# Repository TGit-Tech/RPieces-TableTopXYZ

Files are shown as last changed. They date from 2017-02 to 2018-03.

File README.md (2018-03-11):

-----------------------------------------------------------------------------------
# RPieces-TableTopXYZ
-----------------------------------------------------------------------------------
A Simple and Printable TableTop XYZ Motion Frame using 28BYJ-48 Unipolar Stepper
Motors.

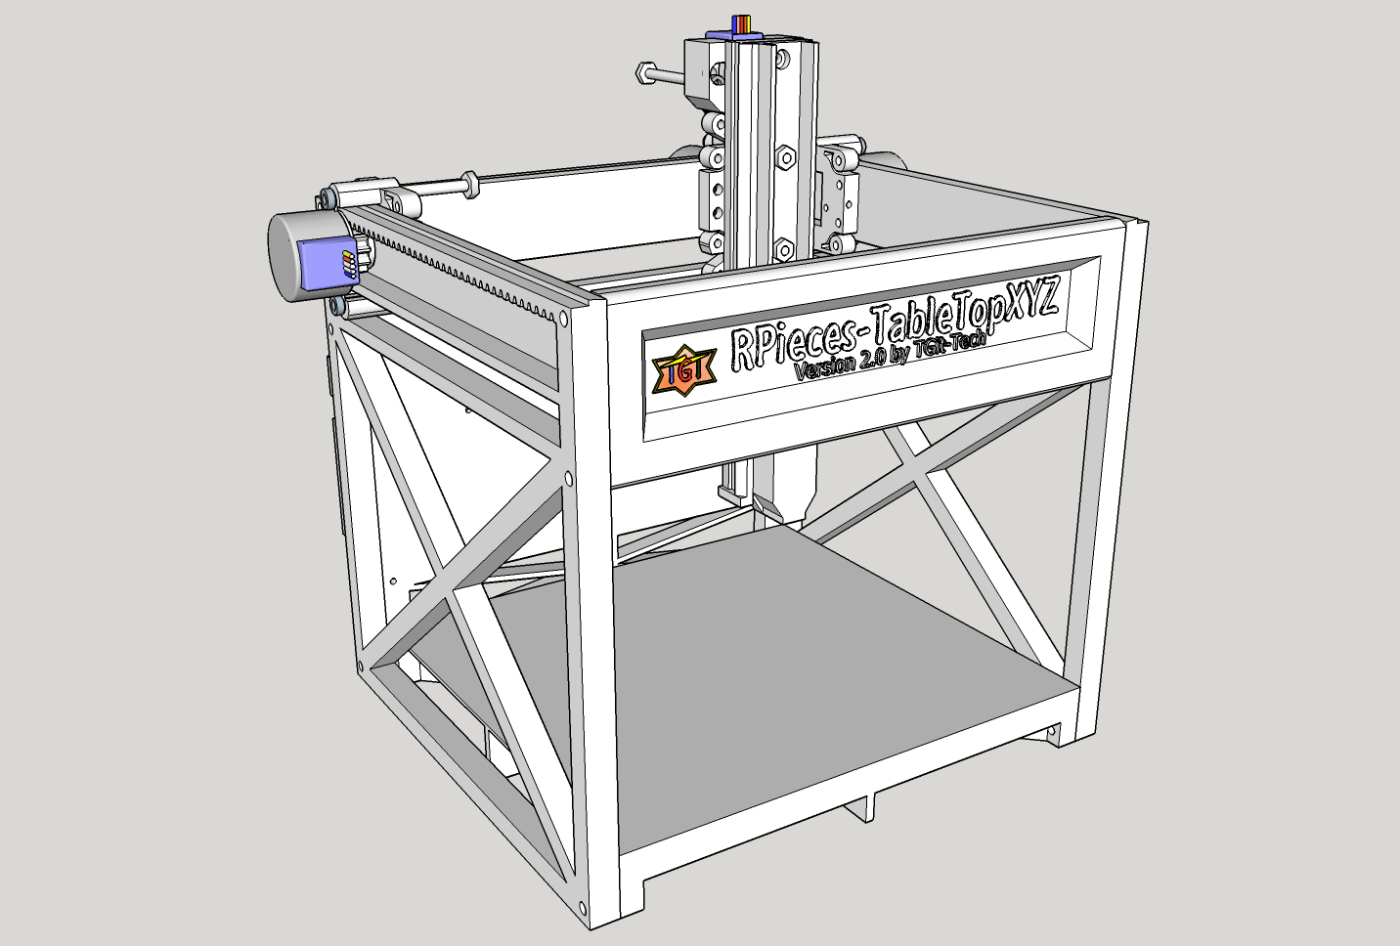
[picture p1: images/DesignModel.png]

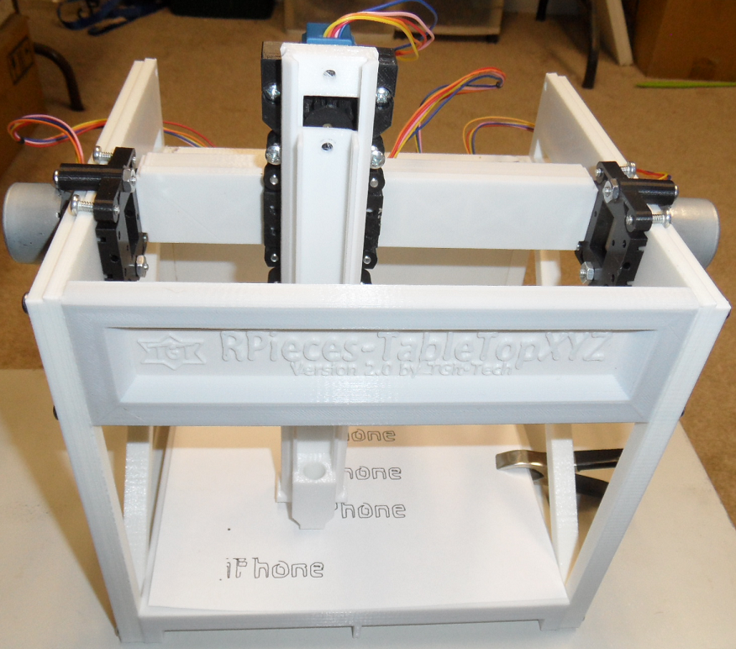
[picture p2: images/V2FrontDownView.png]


The RPieces TableTopXYZ Frame is a project that will attempt to create a simple one
day build of an all in one 3D Printer, Mill, and Plotter.  The project will minimize
the use of linear bearings in place of 3D Printed Rails and minimize the use of 
timing belts in place of 3D-Printed Pinions ( Thus the R.=Rack & P.=Pinion 
abbreviation in RPieces naming convention )

Example Video @ https://www.youtube.com/watch?v=2BT0keDggYo

-----------------------------------------------------------------------------------
#Project Status
-----------------------------------------------------------------------------------
This is RPieces-TableTopXYZ Version 2.0 Beta;  Version 1.0 was released previously.
Unless issues occur this will be the final Version 2.0

Version 2.0 enhancements include a much more stable frame & carriages.  As can be
seen by the video; the prints are still quite sloppy but the test model was printed
using extremely soft plastic on the carriages.  I'd suggest a little harder plastic
on the carriages than originally suggested in the User Manual.

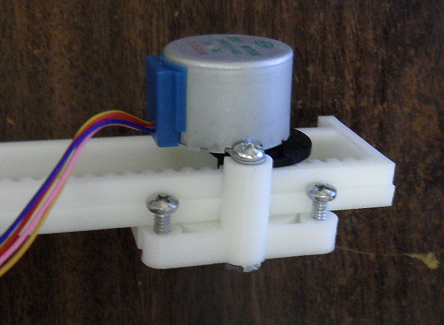
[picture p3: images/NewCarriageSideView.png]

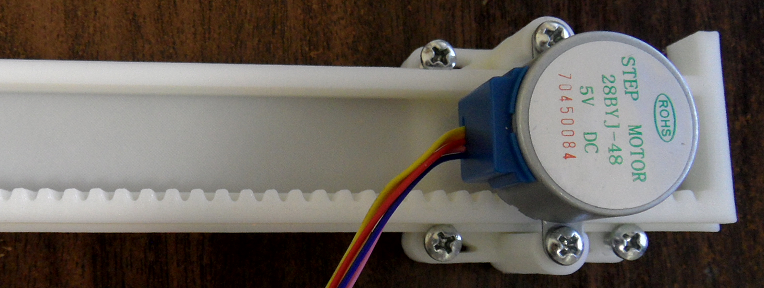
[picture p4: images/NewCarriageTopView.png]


-----------------------------------------------------------------------------------
#Cost and Materials
-----------------------------------------------------------------------------------
Building this project requires

    - (1) 3D Printer with a build surface of at least 190mm x 190mm   ... $N/A
    - (1) Arduino UNO or NANO / half breadboard / jumper kit          ... $ 6.95
    - (4) 28BYJ-48 Stepper Motors with ULN2003 Drivers                ... $ 9.90
    - (~20) Male to Female Dupont jumpers                             ... $ 1.60
    - (1) 5Vdc Wall-module Power Supply adapter at ~2A                ... $ 2.15
    - (12) #6-32 x 1/2" Long Machine Screws                           ... $ 0.24
    - (10) #6-32 x 3/4" Long Machine Screws                           ... $ 0.20
    - (8) #6-32 x 1-1/2" Long Machine Screws                          ... $ 0.16
    - (7) #6-32 x 3/4" Long Machine Screws                            ... $ 0.14
    - (2) #6-32 x 1-1/2" Long Machine Screws                          ... $ 0.06
    - (24) #6 x 3/4" Sheet Metal Screws                               ... $ 0.48
    - (20) #4 x 3/8" Sheet Metal Screws                               ... $ 0.40
    - (10) Corresponding hex nuts (#6) for machine screws             ... $ 0.20
    - Modified GRBL Firmware @ https://github.com/tgit23/GRBL-28byj-48
    - Grbl Controller Software @ http://zapmaker.org/projects/grbl-controller-3-0/

TOTAL ESTIMATED COST (including filament): $33.93
Detailed items/cost inside the Assembly document linked below.

-----------------------------------------------------------------------------------
#Getting Started
-----------------------------------------------------------------------------------
Assembly document can be found @ https://github.com/tgit23/RPieces-TableTopXYZ/blob/master/docs/RPieces-TableTopXYZ-Version2-User-Assembly.pdf

I.e. /docs/RPieces-TableTopXYZ-Version2-User-Assembly.pdf

Before trying to control the model;  Setup the parameters of 'grbl' firmware through
the 'grbl controller' command interface by entering the following commands.

    - $0=30
    - $100=100
    - $101=100
    - $102=100
    - $110=550
    - $111=550
    - $112=550
    - $120=100
    - $121=100
    - $122=100
    
You can now load a file from the \nc-examples folder into grbl controller for unit
testing.

-----------------------------------------------------------------------------------
CONTRIBUTING
-----------------------------------------------------------------------------------
Anyone interested in joining this project can email
tgit28@gmail.com with a return email address.  Details of what can
be done and what needs done can be negotiated from there.

We'd really appreciate any extra man-power we can gather..

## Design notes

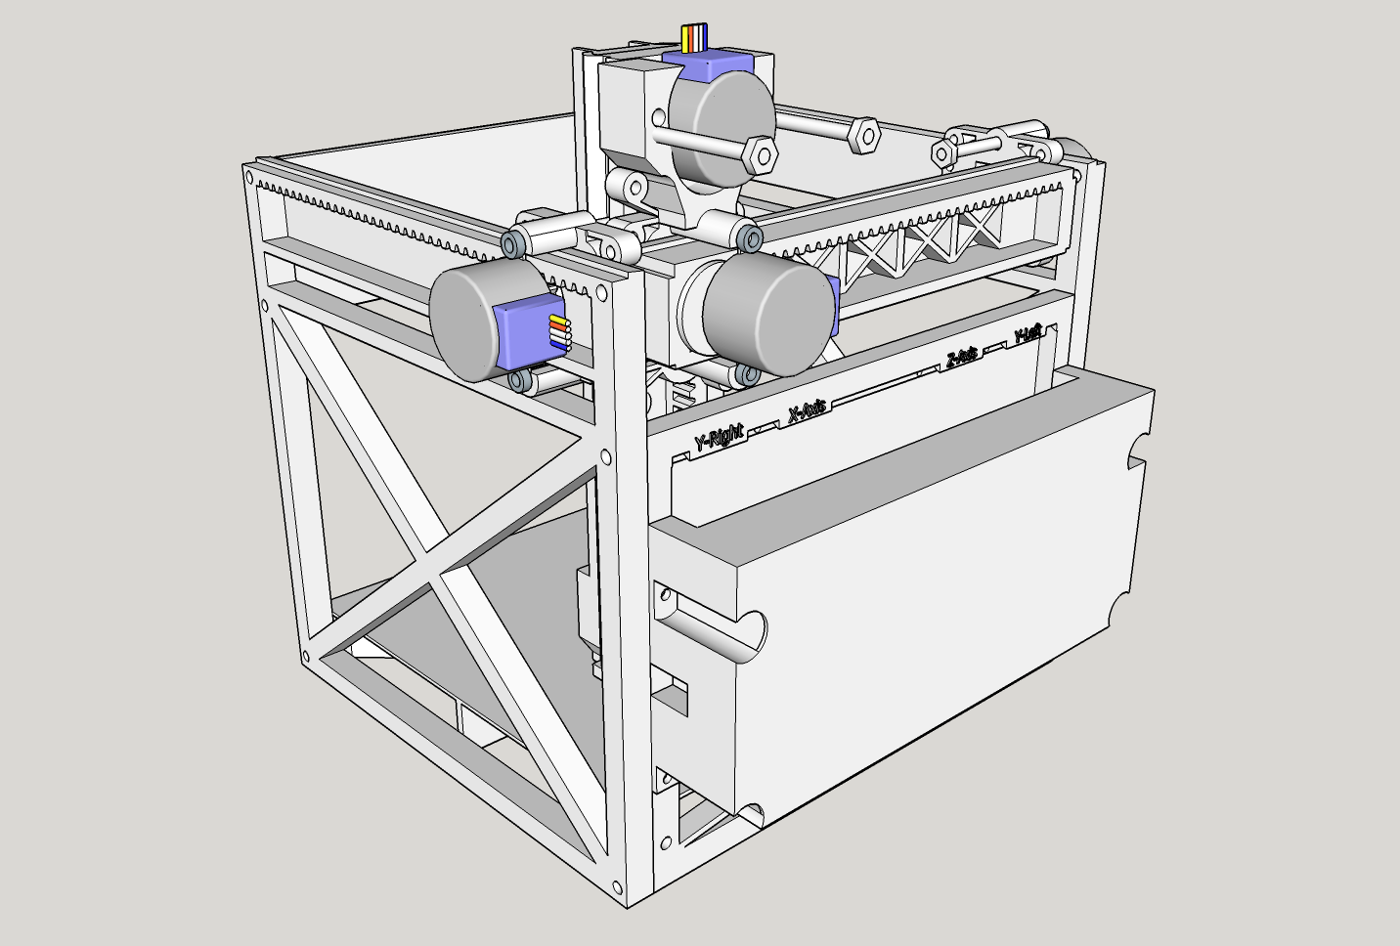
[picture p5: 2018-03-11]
images/DesignModel-Back.png

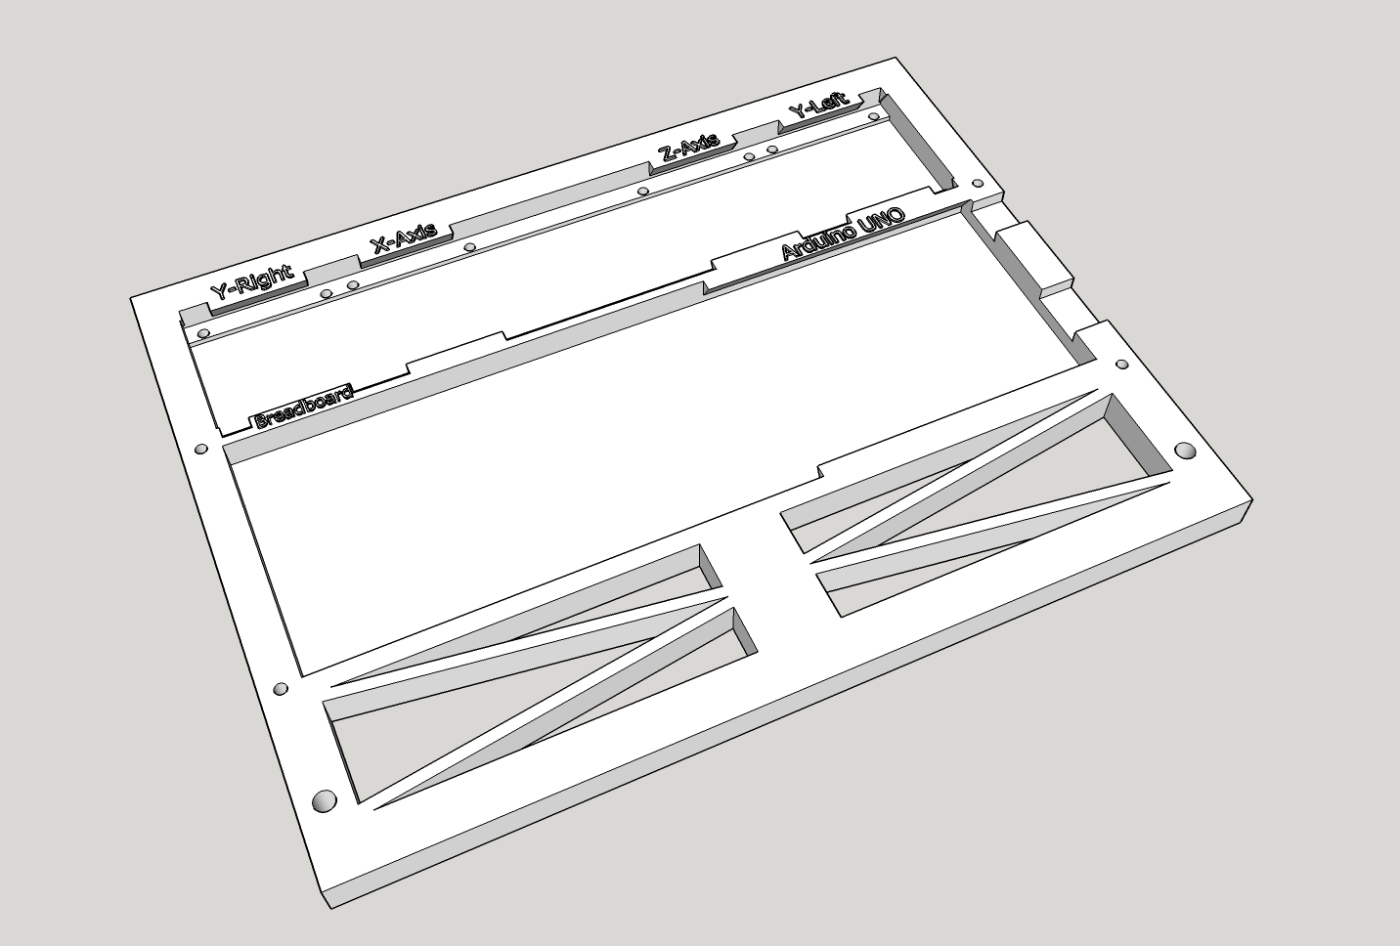
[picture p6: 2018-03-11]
images/Back.png

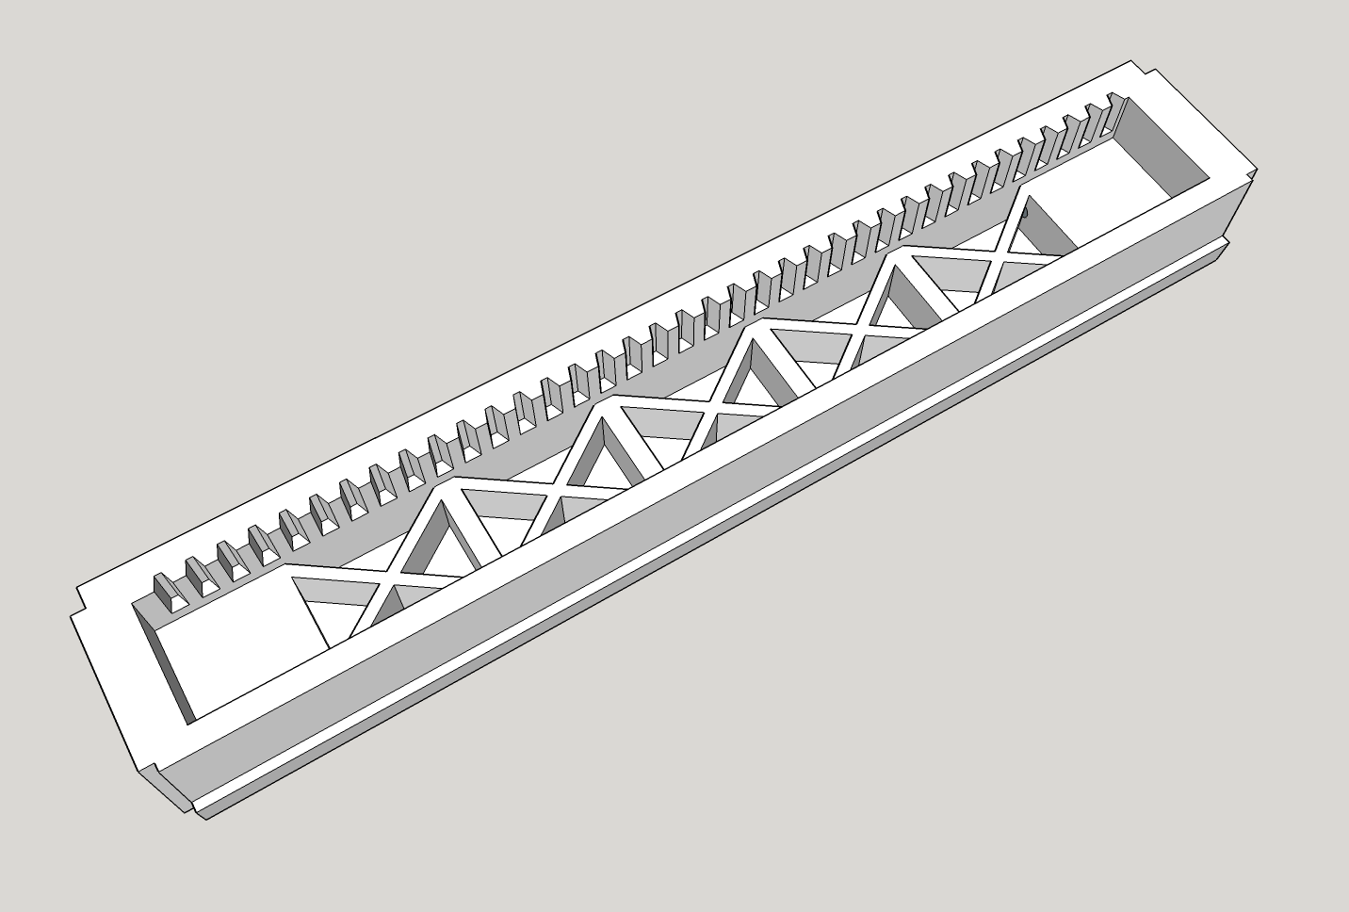
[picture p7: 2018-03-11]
images/X-Rack.png

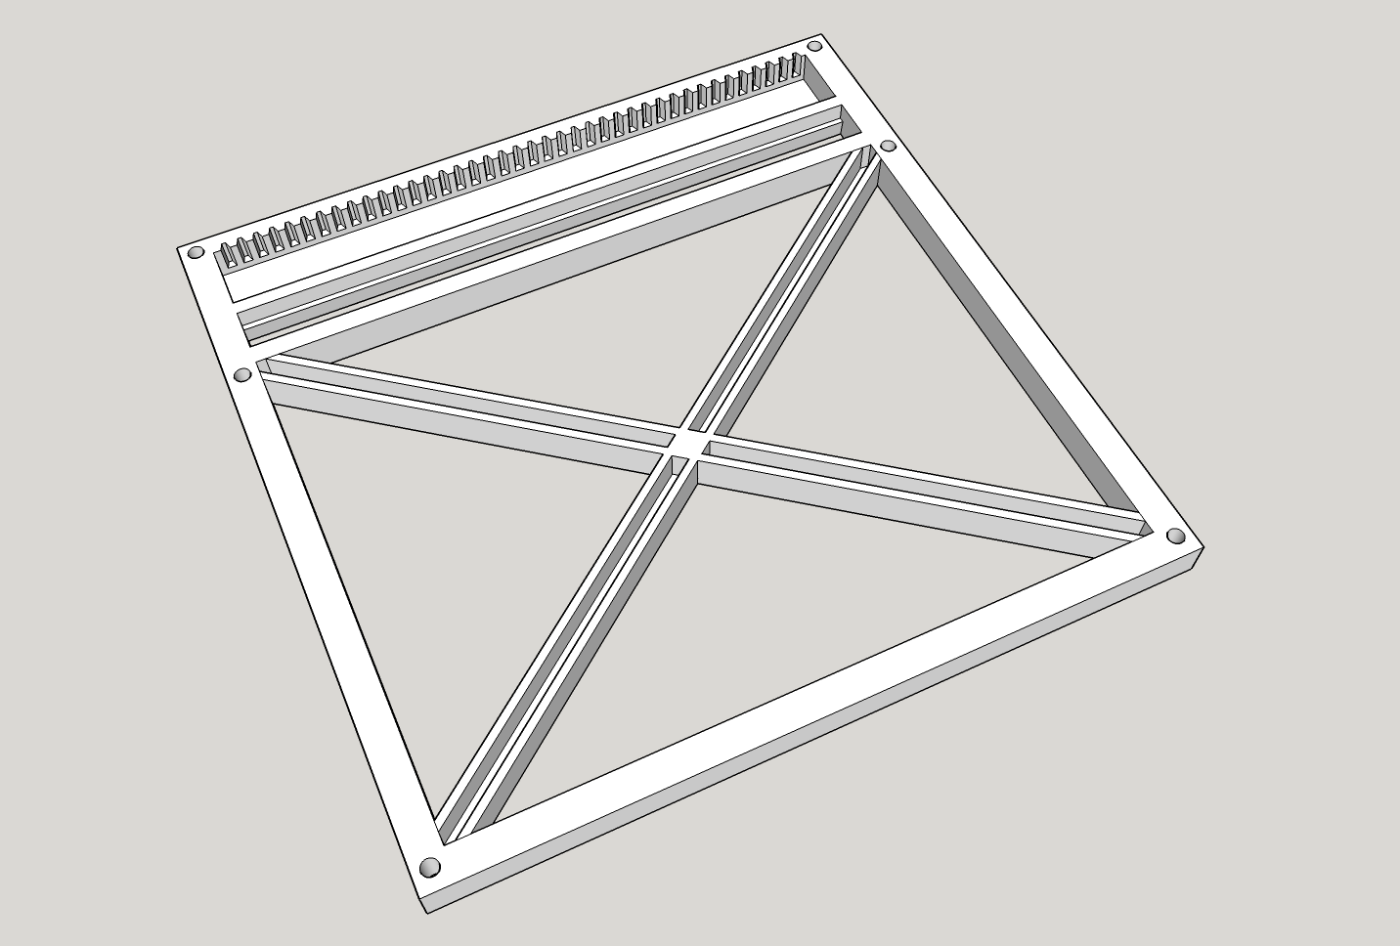
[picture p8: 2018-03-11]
images/Side.png

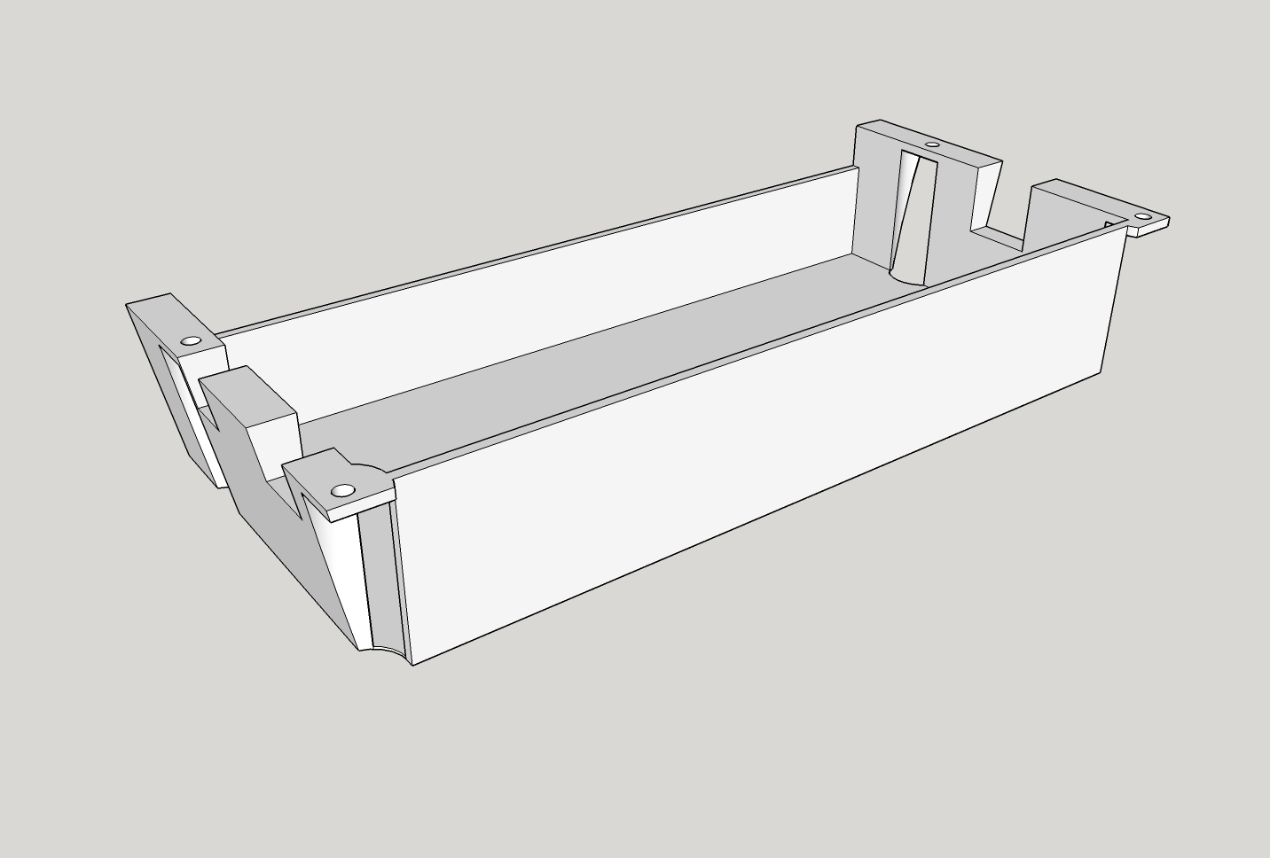
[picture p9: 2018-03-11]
images/BackCover.png

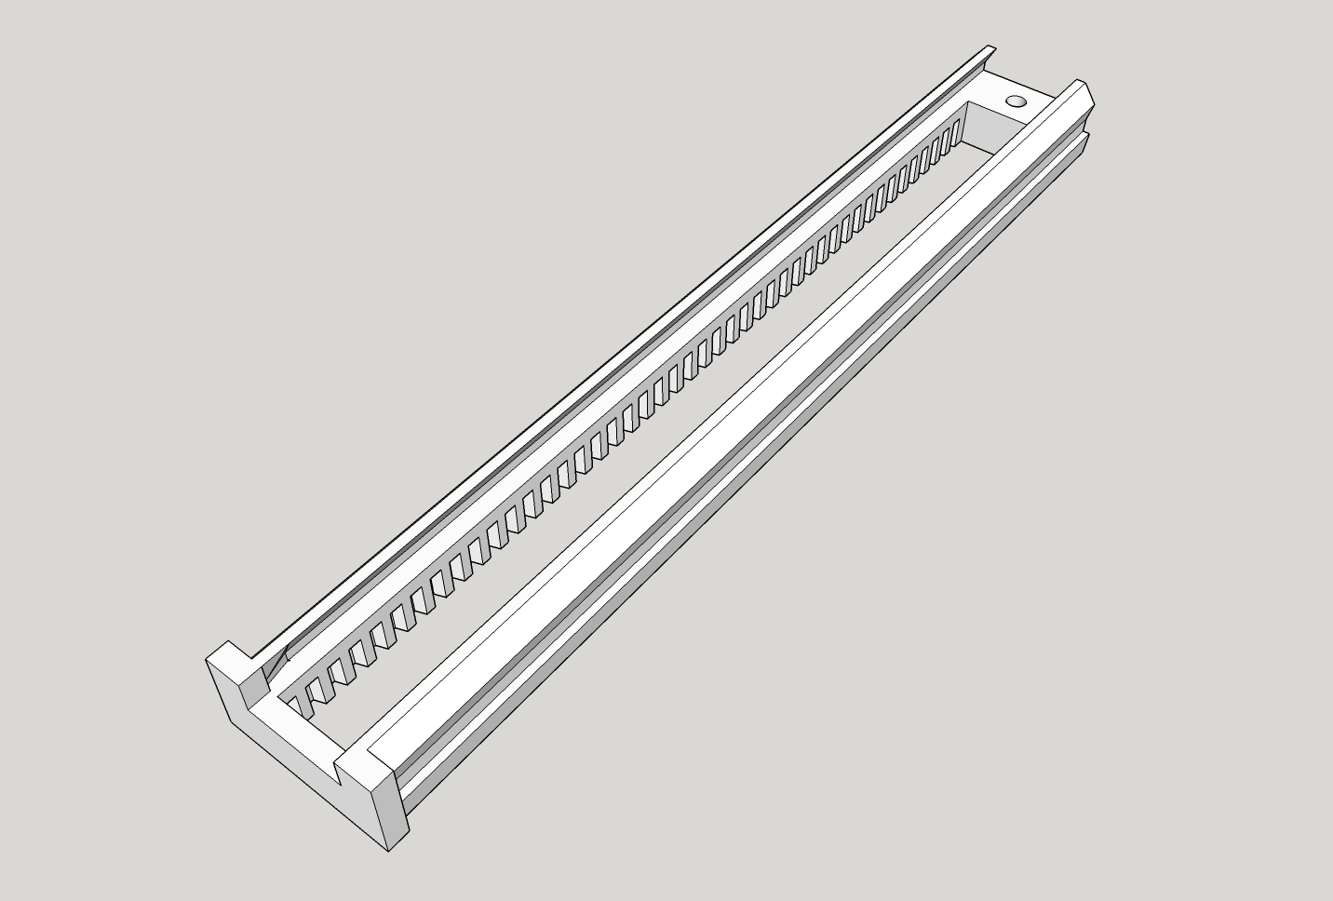
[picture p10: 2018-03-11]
images/Z-Rack.png

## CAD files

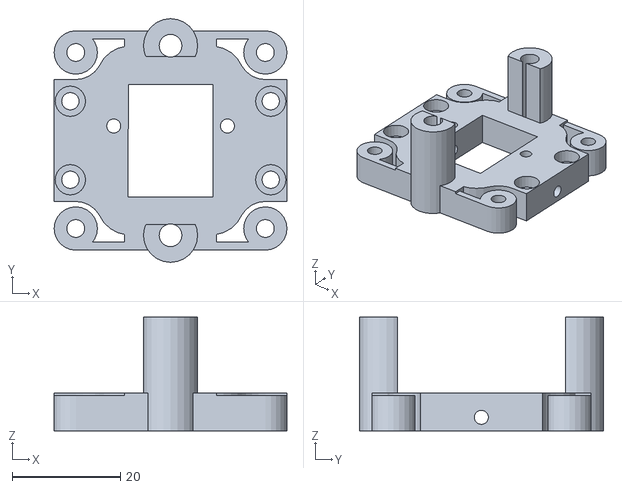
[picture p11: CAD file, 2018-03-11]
Pieces-STL/Y-Carriage.stl
43.0 x 45.0 x 21.0

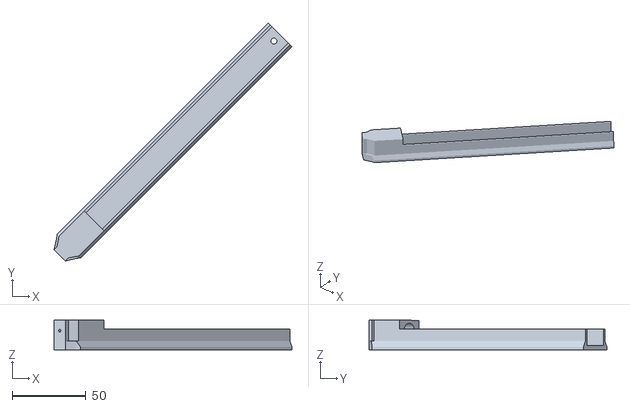
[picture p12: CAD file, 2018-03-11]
ToolHeads-STL/ToolHead-PilotRazorPointPen.stl
161.1 x 161.1 x 20.0

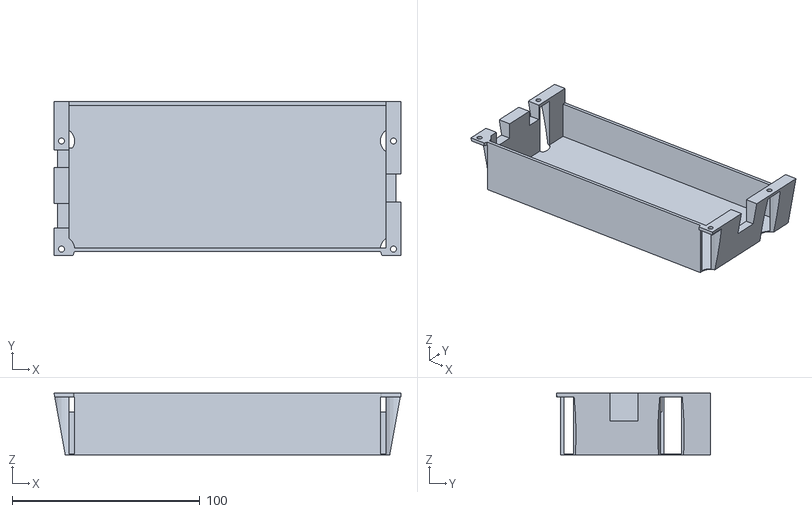
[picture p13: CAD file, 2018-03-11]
Pieces-STL/BackCover.stl
185.0 x 82.0 x 33.0

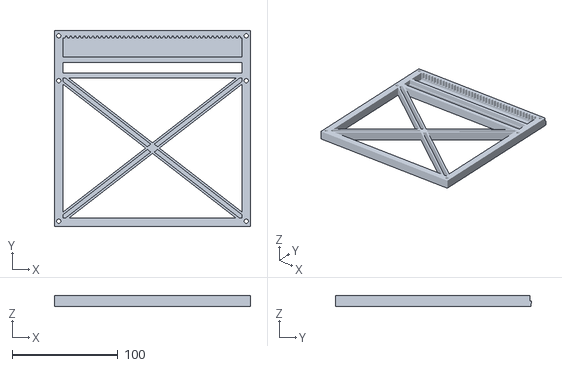
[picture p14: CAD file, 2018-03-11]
Pieces-STL/Side.stl
185.0 x 185.0 x 10.0

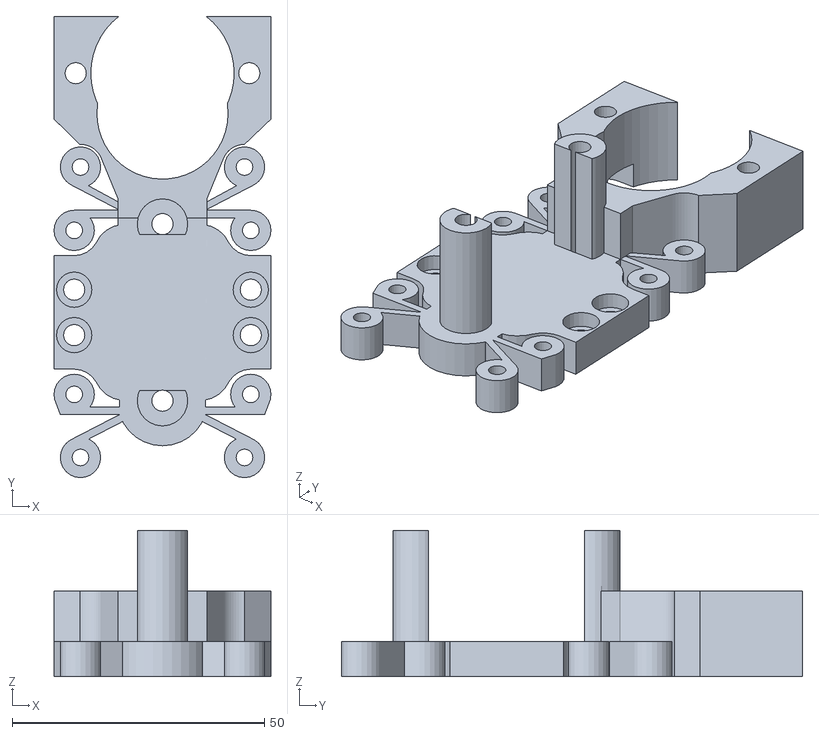
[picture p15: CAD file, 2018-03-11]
Pieces-STL/XZ-Carriage.stl
43.0 x 91.4 x 29.0

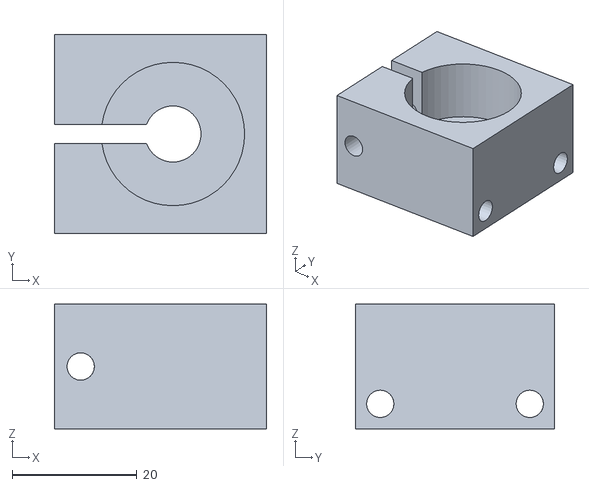
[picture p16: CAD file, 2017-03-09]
ToolHeads-STL/ToolHead-MiniDrill.stl
34.0 x 32.0 x 20.0

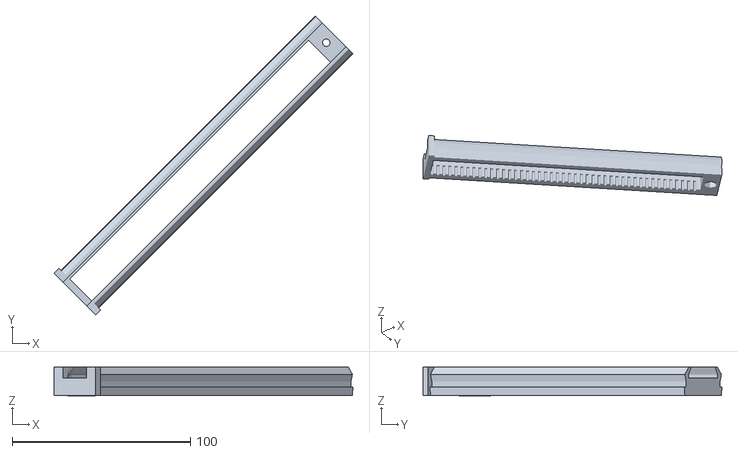
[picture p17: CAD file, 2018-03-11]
Pieces-STL/Z-Rack.stl
167.9 x 167.9 x 16.0

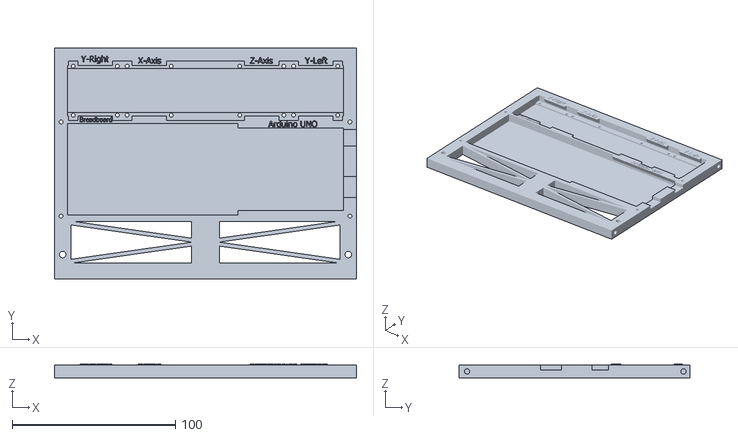
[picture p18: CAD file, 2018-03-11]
Pieces-STL/Back.stl
185.0 x 141.6 x 8.50

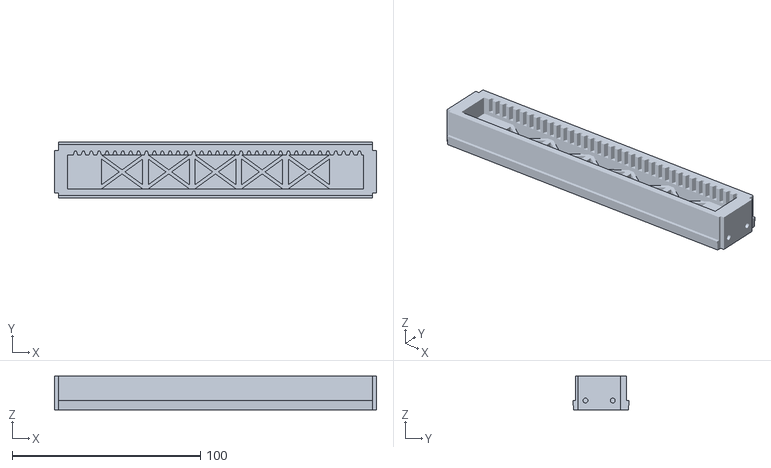
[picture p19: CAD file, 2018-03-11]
Pieces-STL/X-Rack.stl
171.0 x 30.0 x 18.0

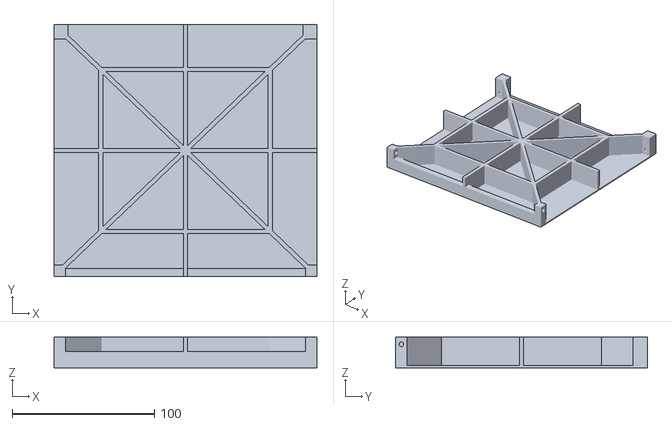
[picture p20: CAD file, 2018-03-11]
Pieces-STL/Bottom.stl
185.0 x 177.0 x 21.5

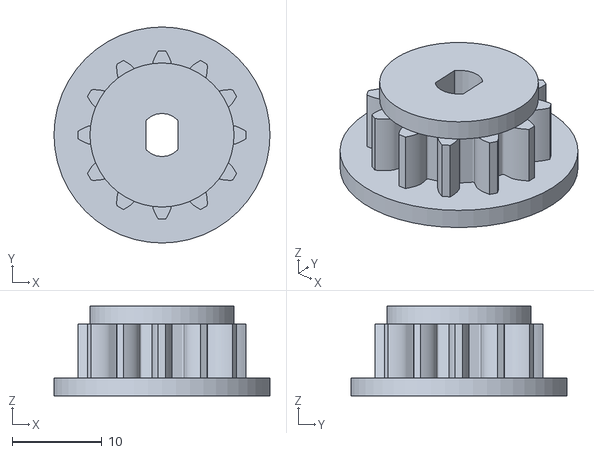
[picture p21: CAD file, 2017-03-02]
Pieces-STL/MotorGear.stl
24.0 x 24.0 x 10.0

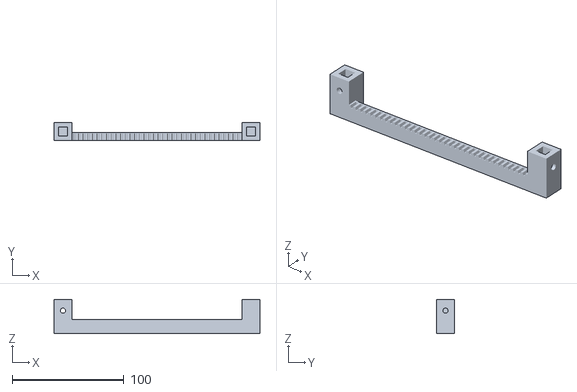
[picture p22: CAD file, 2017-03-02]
Pieces-STL/Y-Rack-Left.stl
184.0 x 16.0 x 30.5

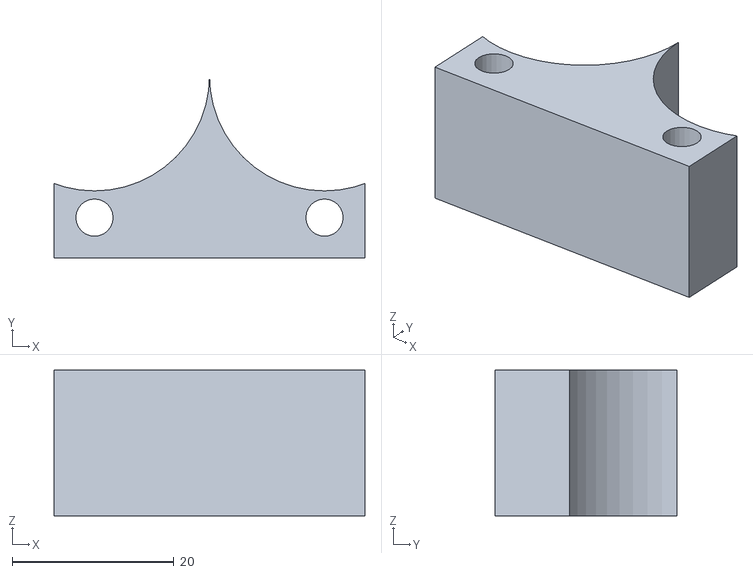
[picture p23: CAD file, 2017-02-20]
Pieces-STL/XYMotorTie.stl
38.4 x 22.5 x 18.0

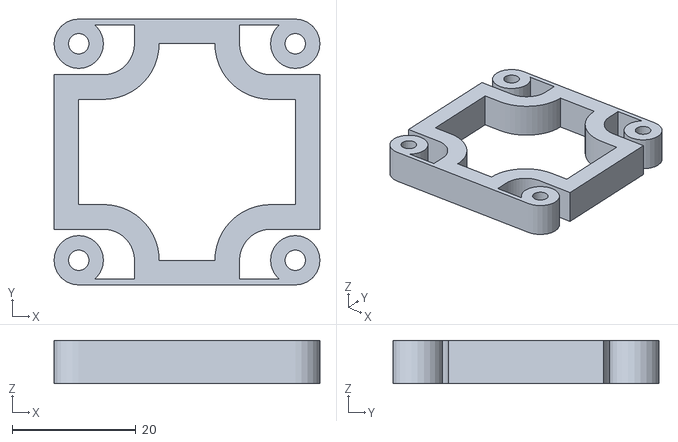
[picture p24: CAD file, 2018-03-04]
ToolHeads-STL/ScrewHead-Slider.stl
43.0 x 43.0 x 7.00

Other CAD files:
ToolHeads-STL/ScrewHead-Rail.stl
Pieces-SketchUp/Back.skp
Pieces-SketchUp/BackCover.skp
Pieces-SketchUp/Bottom.skp
Pieces-SketchUp/Front.skp
Pieces-SketchUp/MotorGear.skp
Pieces-SketchUp/Side.skp
Pieces-SketchUp/X-Rack.skp
Pieces-SketchUp/XZ-Carriage.skp
Pieces-SketchUp/Y-Carriage.skp
Pieces-SketchUp/Z-Rack.skp
ToolHeads-SketchUp/ScrewHead-Rail.skp
ToolHeads-SketchUp/ScrewHead-Slider.skp
ToolHeads-SketchUp/ToolHead-MiniDrill.skp
ToolHeads-SketchUp/ToolHead-PilotRazorPointPen.skp
ToolHeads-SketchUp/ToolHead-Template.skp
docs/DesignModel.skp

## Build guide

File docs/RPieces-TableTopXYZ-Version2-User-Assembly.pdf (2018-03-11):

# RPieces - TableTopXYZ

## User and Assembly Manual

For Version 2.0

Written By: TGit-Tech (03/2018) Feel free to use: no strings attached (text content only / images respectfully referenced)

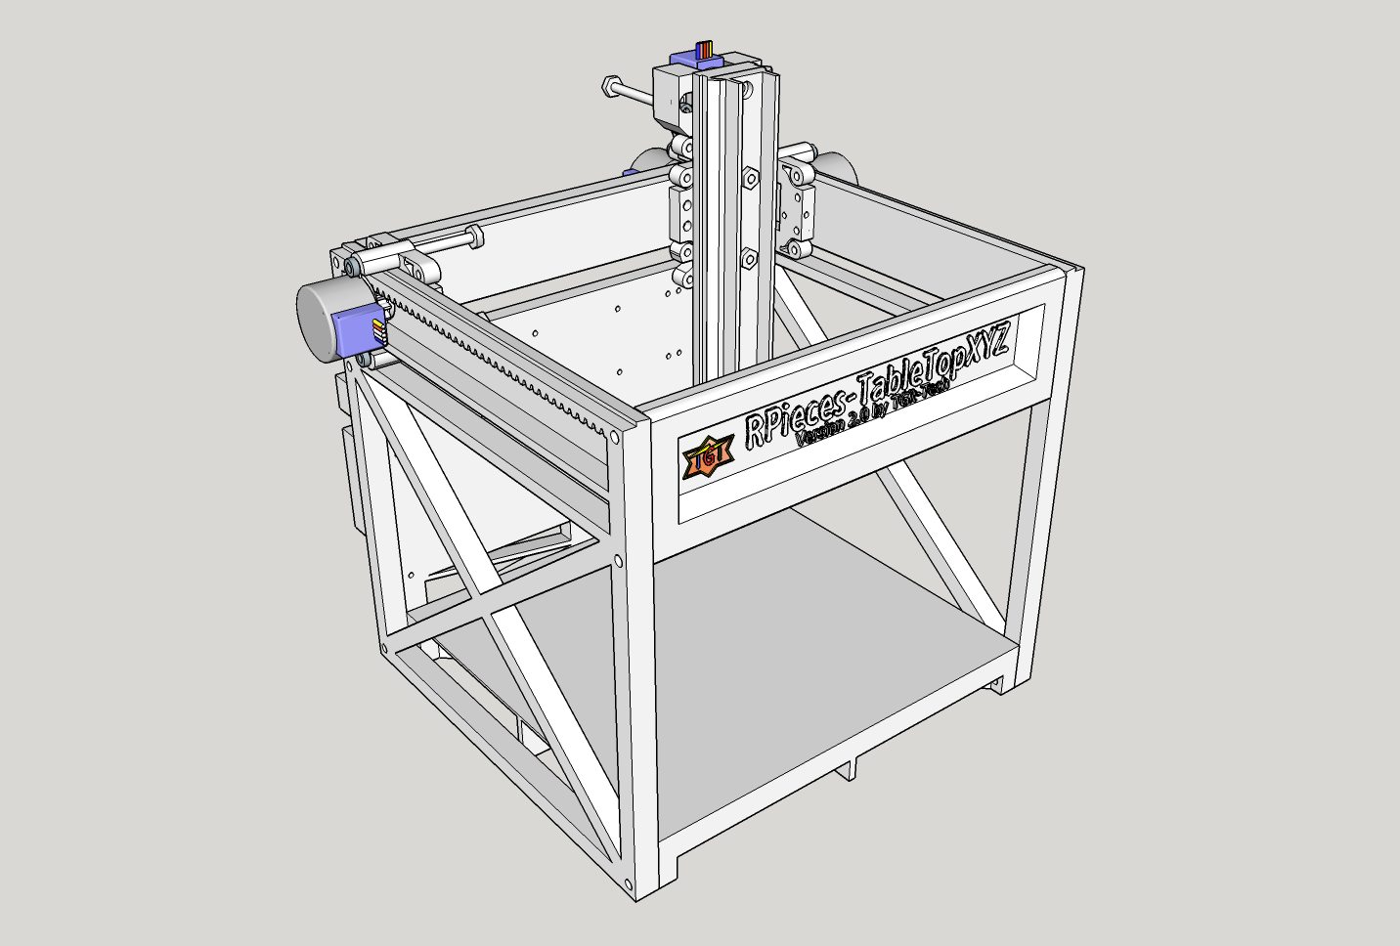
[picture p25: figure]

# Table of Contents

( 1. INTRODUCTION :: INTRODUCTION :: INTRODUCTION ) Page -2-

### 1. INTRODUCTION

The “RPieces – TableTopXYZ ” project's goal is to provide a simple and almost entirely printable motion frame for various usages. Possibly including 3d printing, plotting and minor milling. The platform can also be used in testing software, firmware or just testing model-creation on a physical unit before sending it to a much larger commercial unit.

The project is Open Source and Resides at: https://github.com/TGit-Tech/RPieces-TableTopXYZ
This documentation resides at: https://github.com/TGit-Tech/RPieces-TableTopXYZ/tree/master/docs

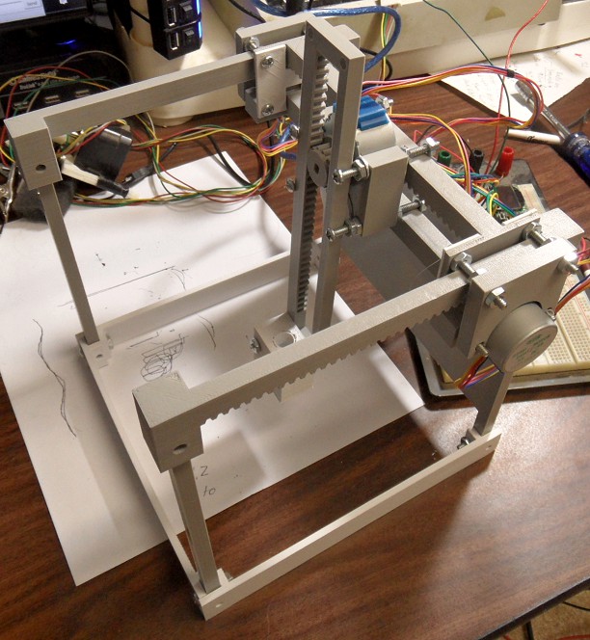
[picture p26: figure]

( 2. BILL OF MATERIALS - $33.93 :: BILL OF MATERIALS - $33.93 :: BILL OF MATERIALS - $33.93 ) Page -3-

### 2. BILL OF MATERIALS - $33.93

### 2.1 Tools (N/A)

The following tools are required to build the project components
✔ 3D-Printer ( With a 185mm x 185mm or larger XY Build Envelope ) ✔ Phillips head screw driver and 5/16 nut driver or wrench

### 2.2 Power Supply ( $2.15 )

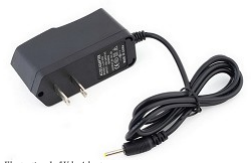
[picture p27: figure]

Illustration 1: 5Vdc Adapter

✔ ( 1 ) 5Vdc ( Possibly up to 7Vdc – I'm using a 6Vdc 700mA ) Power Adapter @ 400mA or greater ( $2.15 )
◌ https://www.aliexpress.com/item/1pcs-Universal-for-IC-Power-Adapter-AC-Charger-5V-2A-DC-2-5mm-US-for-Android/32581666097.html

### 2.3 Electronic Control ( $18.45 )

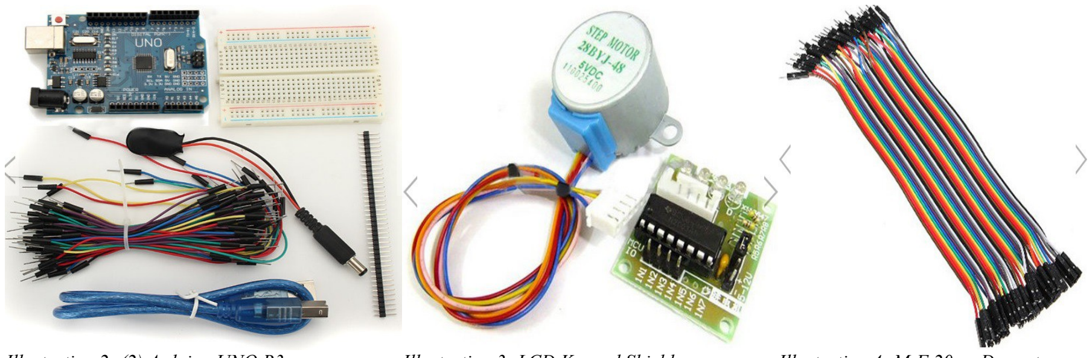
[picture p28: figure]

Illustration 2: (2) Arduino UNO R3 | Illustration 3: LCD Keypad Shield | Illustration 4: M-F 20cm Dupont

✔ ( 1 ) UNO R3 or NANO Atmega328P Module, Mini Breadboard & Jumpers ( $6.95/ea )
◌ https://www.aliexpress.com/item/Starter-Kit-for-Uno-R3-Bundle-of-5-Items-Uno-R3-Breadboard-Jumper-Wires-USB-Cable/32813470187.html

✔ ( 4 ) 28BYJ-48 5V DC Step Motor with ULN2003 Driver Board ( $9.90/per5 )
◌ https://www.aliexpress.com/item/NEW-5pcs-lot-Gear-Stepper-Motor-28BYJ-48-DC-5V-ULN2003-Driver-Test-Module-Board-For/32826285578.html ◌ Resources
- 28BYJ Data-sheet http://www.sensors.co.nz/datasheet/28BYJ-48%20Stepper%20Motor.pdf
- ULN2003 Data-sheet http://www.ti.com/lit/ds/symlink/uln2003a.pdf

✔ ( ~40 ) 20 cm Male to Female DuPont Jumpers ( $1.60 )
◌ https://www.aliexpress.com/item/Dupont-line-40pcs-20cm-male-to-female-jumper-wire-Banana-pro-Dupont-cable-support-Raspberry-pi/32393258299.html

2.4 3D Parts & Fasteners ($13.33)

Below is the list of the Parts that need to be printed with a 3D-Printer in the order of assembly; so you can print them in the order shown and assemble them as they finish. Default printer settings are below; but check the per-part details below for any part-specific setting if one may exist .

✔ Parts were printed on an Anet A8 3D-Printer using Cura with the following settings
◌ Layer Height = 0.2

( 2.4 BILL OF MATERIALS - $33.93 :: 3D Parts & Fasteners ($13.33) :: 3D Parts & Fasteners ($13.33) ) Page -4-

◌ Shell Thickness = 1.6
◌ Fill Density = 100%
◌ Print Speed = 60
◌ Support = None

✔ Suggestions
◌ Bed leveling is extra important with any Rack-Gear containing prints -- to ensure a fairly consistent width across the entire tab-out. ◌ Use hairspray, tape or any preferred method that keeps large prints on the build plate – uneven builds will cause massive faults.
◌ Parts that hold structure are PLA preferred due to its non-curling and non-flexible (brittle) attributes.
- I've especially been impressed with iFun and PxMallion for cheap structurally sound PLA filament brands
◌ Carriage parts are ABS preferred due to their flexible tension-ed slide screws but PLA should work fine.
- eSun PLA+ filament makes a nice balance between PLA and ABS for such parts.
◌ Push all stepper motors towards the drive rail before tightening -- to make a snug gear to rail connection ( reduces slop ).
QTY | Part Picture Part Filename Grams of Filament | Attaches To | Fasteners (!Per-Part!)*QTY | Est. Costs Per-Part PLA Cost @ $15/Kg roll www.boltdepot.com @100-lots | Total Cost
4 | MotorGear.stl 3-grams PLA preferred | 28BYJ-Motor | N/A – Pressed On | $0.04 Plastic | $0.18
1 | X-Rack.stl 58-grams PLA preferred | N/A | N/A See XZ & Y-Carriage | $0.87 Plastic | $0.87
1 | XZ-Carriage.stl 30-grams ABS preferred | X-Rack X-Motor Z-Rack Z-Motor | (4)#6 x 3/4” Sheet Metal Screws [$0.02/ea] (2)#6-32 x 1.5” [$0.03/ea] (4)#6-32 x 1/2” [$0.02/ea] (2)#6-32 x 3/4” [$0.02/ea] | $0.45 Plastic $0.26 Fasteners | $0.71
2 | Y-Carriage.stl 12-grams ABS preferred | X-Rack Full-Side Y-Motor | (2)#4 x 3/4” Sheet Metal Screws [$0.03/ea] (4)#6-32 x 1/2” Machine Screws [$0.02/ea] (2)#6-32 x 1” Machine Screws [$0.03/ea] | $0.18 Plastic $0.20 Fasteners | $0.76

Assembly Instructions for parts above @ #3.1.XZ-Carriage|outline
1 | Back.stl 109-grams PLA preferred | (4)ULN2003 Arduino (2)Side | (16) #4 x 3/8” Sheet Metal Screws [$0.02/ea] [Optional] – Attaching ULN2003 with screws makes them much more stable but not required. N/A See Side for fasteners | $1.63 Plastic $0.32 Fasteners | $1.95
1 | BackCover.stl [!Optional Part!] 54-grams W/Supports! | Back | (4)#4 x 3/8” Sheet Metal Screws [$0.02/ea] | $0.81 Plastic $0.08 Fasteners | $0.89

Assembly Instructions for parts above @ #4.ELECTRONICS|outline 1

Front.stl
60-grams

(2)Side N/A See Side for fasteners

$0.90 Plastic
$0.08 Fasteners

$0.98

( 2.4 BILL OF MATERIALS - $33.93 :: 3D Parts & Fasteners ($13.33) :: 3D Parts & Fasteners ($13.33) ) Page -5-

| PLA preferred
2 | Side.stl 115-grams PLA preferred | Back Front Bottom | (2)#6 x 3/4” Sheet Metal Screws [$0.02/ea] (2)#6 x 3/4” Sheet Metal Screws [$0.02/ea] (1)#6 x 3/4” Sheet Metal Screw [$0.02/ea] | $1.72 Plastic $0.12 Fasteners | $3.68
1 | Bottom.stl 184-grams PLA preferred | Back (2)Side | (2)#6 x 3/4” Sheet Metal Screws [$0.02/ea] See Side for fasteners | $2.76 Plastic $0.04 Fasteners | $2.80

Assembly Instructions for parts above @ #3.2.Frame|outline 1

Z-Rack.stl
38-grams
PLA preferred
206mm Long (angle)
N/A | N/A
See XZ-Carriage
$0.57 Plastic | $0.57

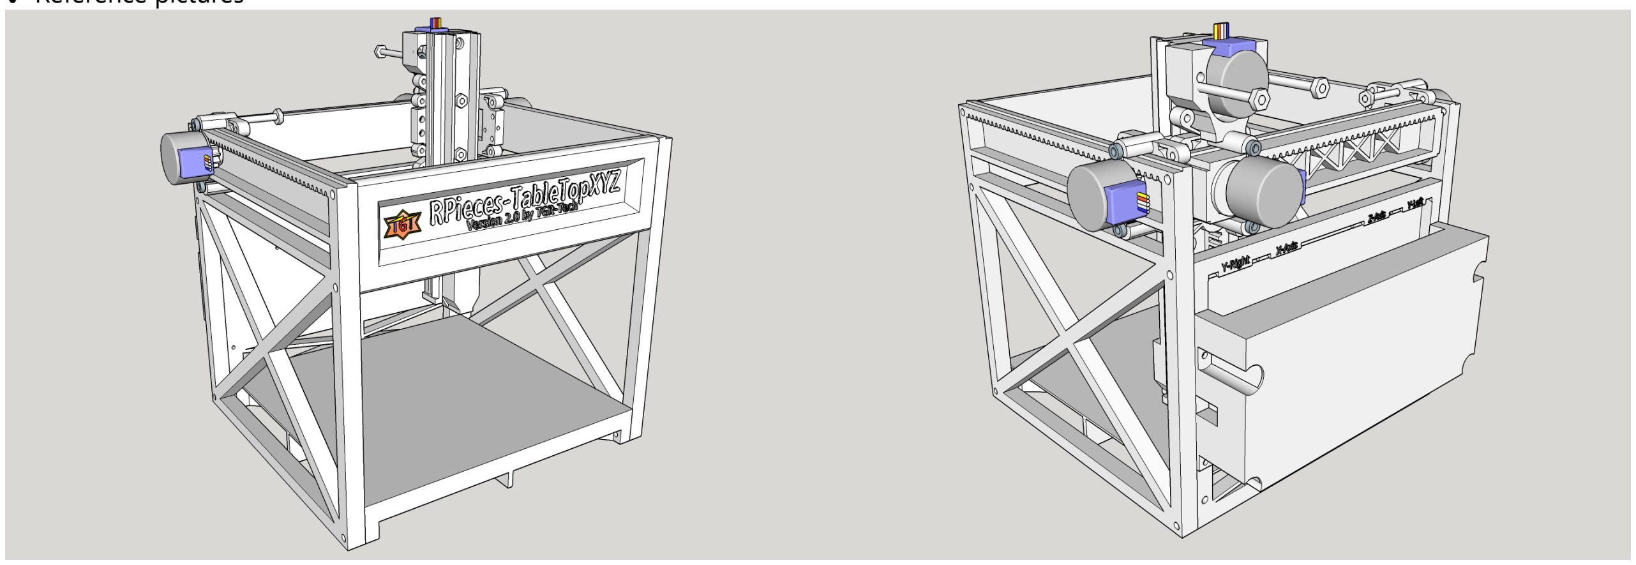
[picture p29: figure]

✔ Reference pictures

( 3. HARDWARE ASSEMBLY :: HARDWARE ASSEMBLY :: HARDWARE ASSEMBLY ) Page -6-

### 3. HARDWARE ASSEMBLY

### 3.1 XZ-Carriage

1. Press (2) MotorGears onto (2) 28BYJ-48 Stepper Motor

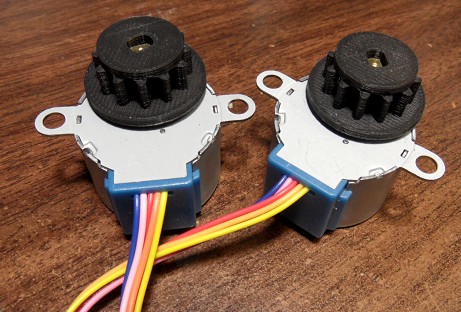
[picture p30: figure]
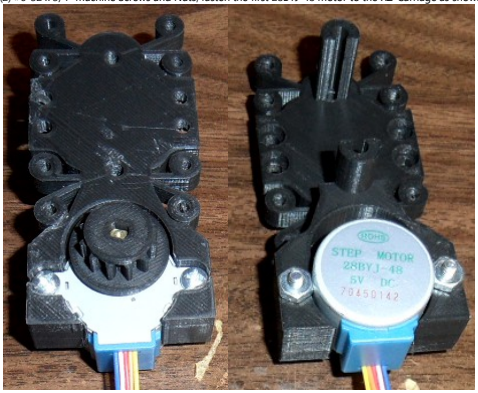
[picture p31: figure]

2. Using (2) #6-32 x 3/4” Machine Screws and Nuts; fasten the first 28BYJ-48 motor to the XZ-Carriage as shown below

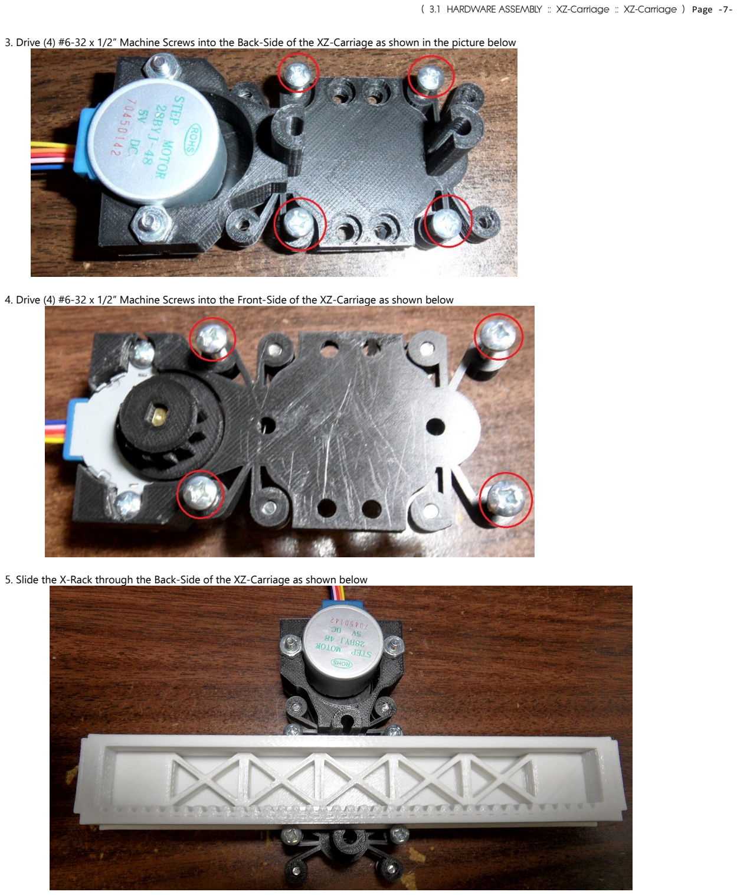
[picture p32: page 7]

( 3.1 HARDWARE ASSEMBLY :: XZ-Carriage :: XZ-Carriage ) Page -7-

3. Drive (4) #6-32 x 1/2” Machine Screws into the Back-Side of the XZ-Carriage as shown in the picture below
4. Drive (4) #6-32 x 1/2” Machine Screws into the Front-Side of the XZ-Carriage as shown below
5. Slide the X-Rack through the Back-Side of the XZ-Carriage as shown below

( 3.1 HARDWARE ASSEMBLY :: XZ-Carriage :: XZ-Carriage ) Page -8-

6. Using (4) #6 x 3/4” Sheet Metal Screws; attach (2) Y-Carriages to each end of the X-Rack with motor mounts pointing out and X-Rack hanging off the back edge of the Y-Carriage as shown below

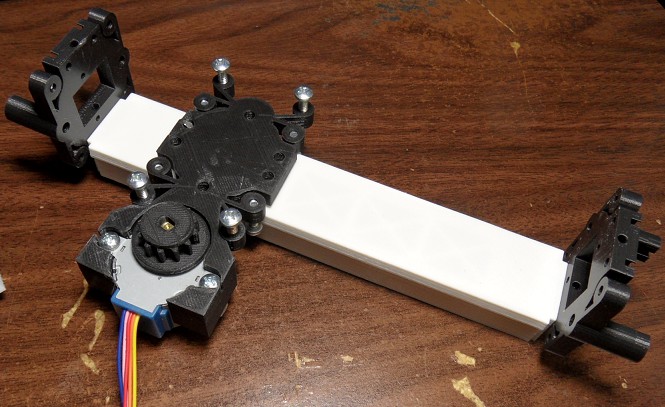
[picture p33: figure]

7. Adjust the (4) XZ-Carriage Rack Screws that hold the X-Rack so the screw touches the Tab-Out
a) Press the X-Rack against the XZ-Carriage to determine how far to tighten
b) Slide the XZ-Carriage across the X-Rack while tightening and be sure there isn't too much friction

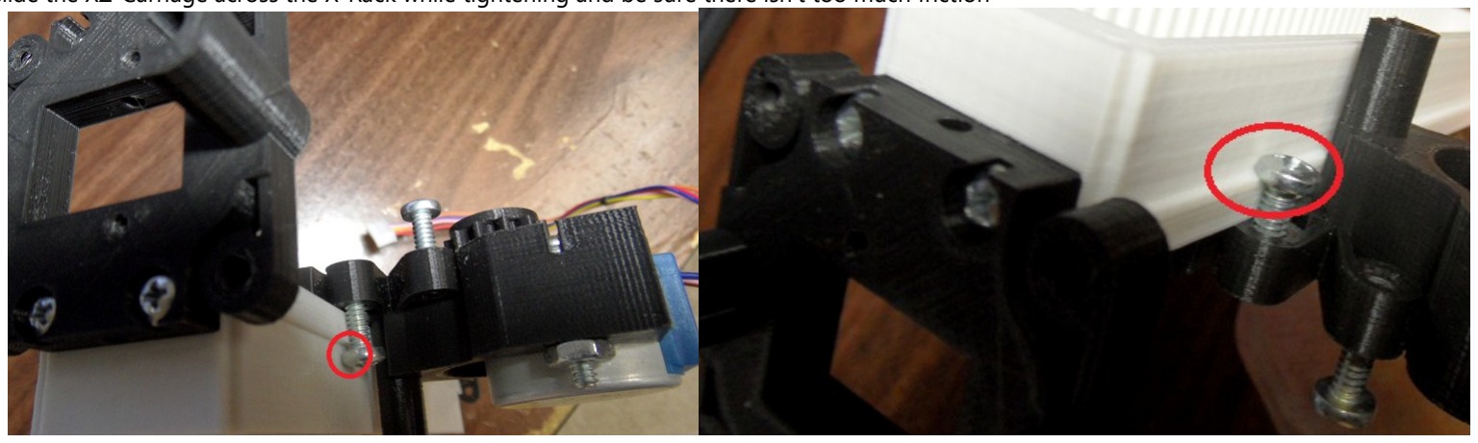
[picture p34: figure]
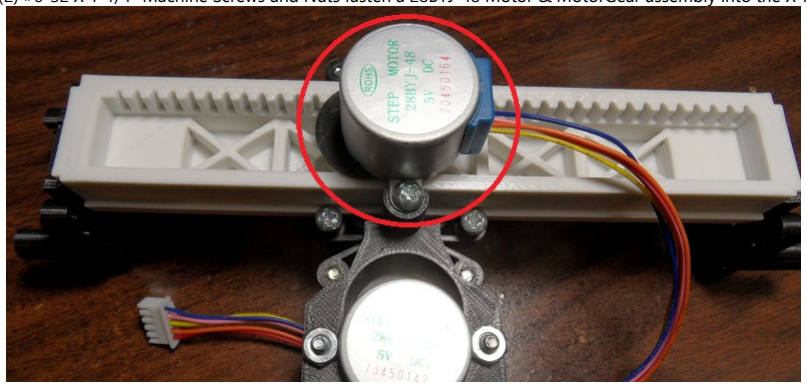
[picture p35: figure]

8. Using (2) #6-32 X 1-1/4” Machine Screws and Nuts fasten a 28BYJ-48 Motor & MotorGear assembly into the X-Rack as shown

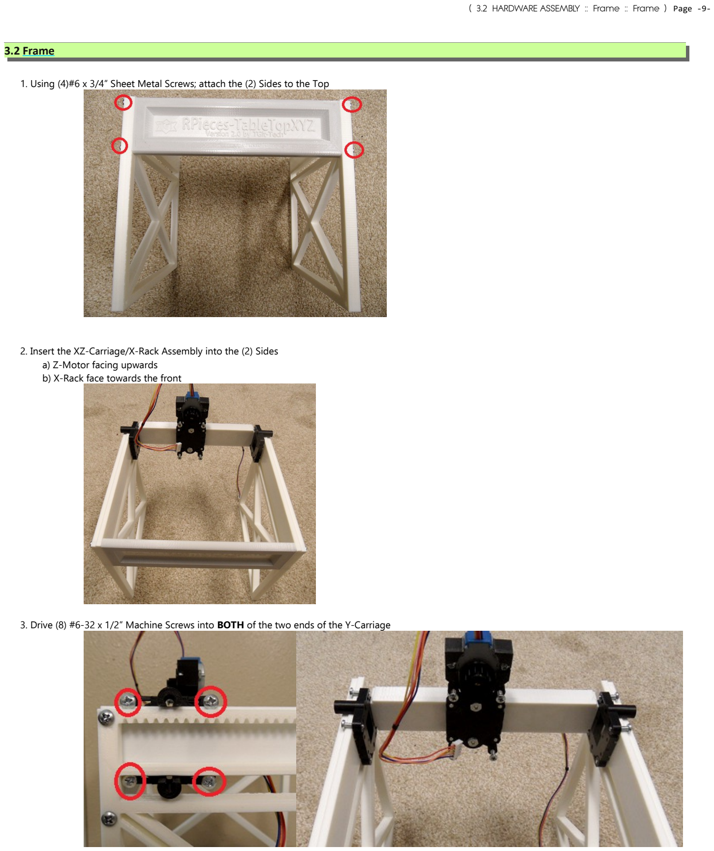
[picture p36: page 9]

( 3.2 HARDWARE ASSEMBLY :: Frame :: Frame ) Page -9-

### 3.2 Frame

1. Using (4)#6 x 3/4” Sheet Metal Screws; attach the (2) Sides to the Top
2. Insert the XZ-Carriage/X-Rack Assembly into the (2) Sides
a) Z-Motor facing upwards
b) X-Rack face towards the front
3. Drive (8) #6-32 x 1/2” Machine Screws into BOTH of the two ends of the Y-Carriage

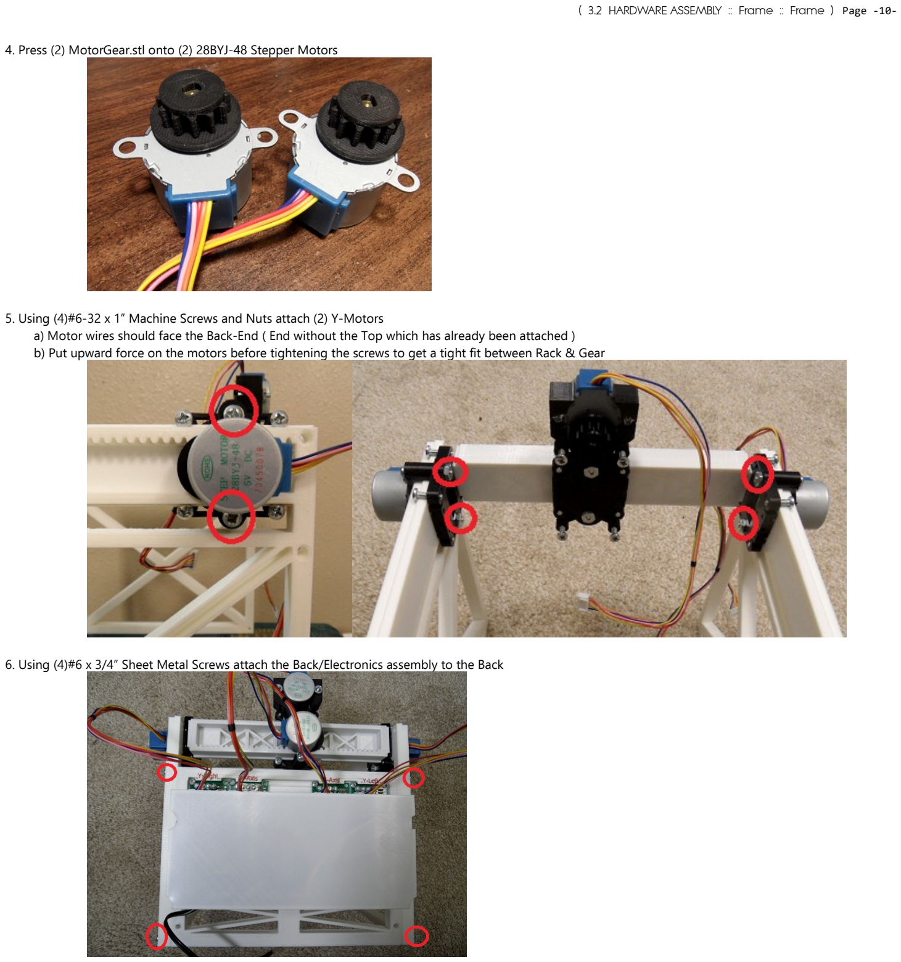
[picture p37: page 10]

( 3.2 HARDWARE ASSEMBLY :: Frame :: Frame ) Page -10-

4. Press (2) MotorGear.stl onto (2) 28BYJ-48 Stepper Motors
5. Using (4)#6-32 x 1” Machine Screws and Nuts attach (2) Y-Motors
a) Motor wires should face the Back-End ( End without the Top which has already been attached )
b) Put upward force on the motors before tightening the screws to get a tight fit between Rack & Gear
6. Using (4)#6 x 3/4” Sheet Metal Screws attach the Back/Electronics assembly to the Back

( 3.2 HARDWARE ASSEMBLY :: Frame :: Frame ) Page -11-

7. Using (4)#6 x 3/4” Sheet Metal Screws attach the Bottom to the sides and the Back
a) Ledge-ed edge of the bottom faces the front

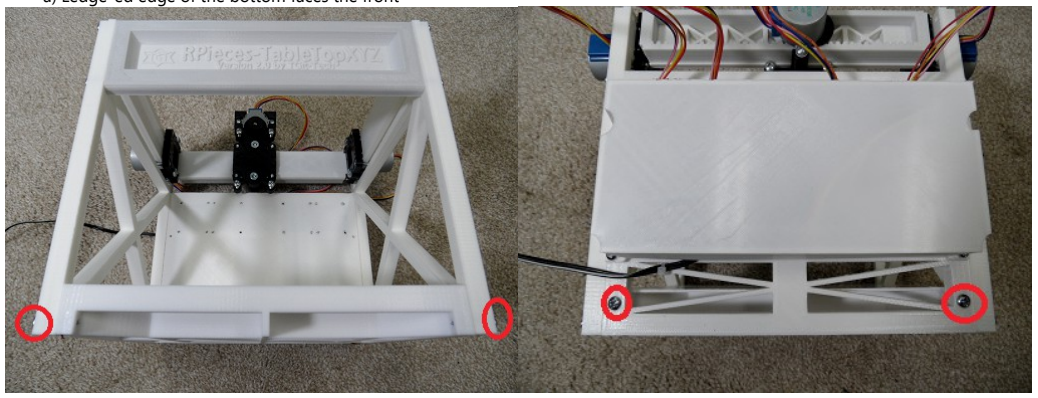
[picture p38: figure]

### 3.3 Z-Rack & Toolheads

1. Position the Z-Rack to center of the XZ-Carriage and attach
a) Try pressing, wiggling or spreading the holding screws a little or pinching the Z-Rack
b) If all else fails remove the XZ-Carriage screws and re-attach them with Z-Rack in place.

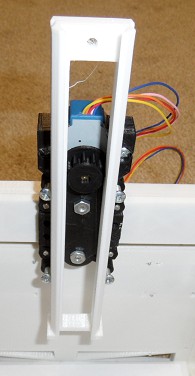
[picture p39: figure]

2. Proceed to pick a Tool-Head in section #6.TOOL-HEADS|outline and slide it into the Z-Rack and apply the (1) #6-32 x 1/2” machine screw and nut.

( 4. ELECTRONICS :: ELECTRONICS :: ELECTRONICS ) Page -12-

### 4. ELECTRONICS

### 4.1 Install Components

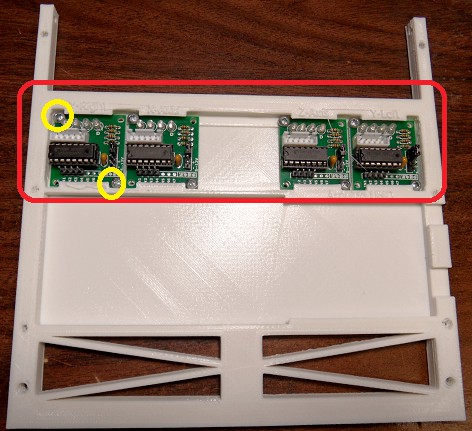
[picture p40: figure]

1. Install (4) ULN2003 Driver Boards into the Back.stl – Optionally; (16)#4 x 3/8” Sheet Metal Screws can be used for stability

( 4.1 ELECTRONICS :: Install Components :: Install Components ) Page -13-

2. Install the Arduino and Breadboard
a) If using Arduino UNO; install the Arduino UNO first then the breadboard
b) If using Arduino Nano; install breadboard first then the Nano positioned over center towards the top

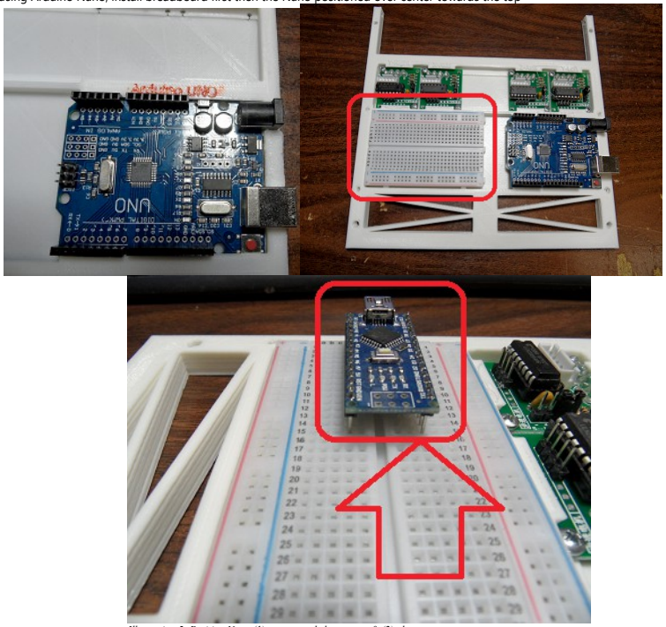
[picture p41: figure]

Illustration 5: Position Nano (1) empty row below center & (2) above

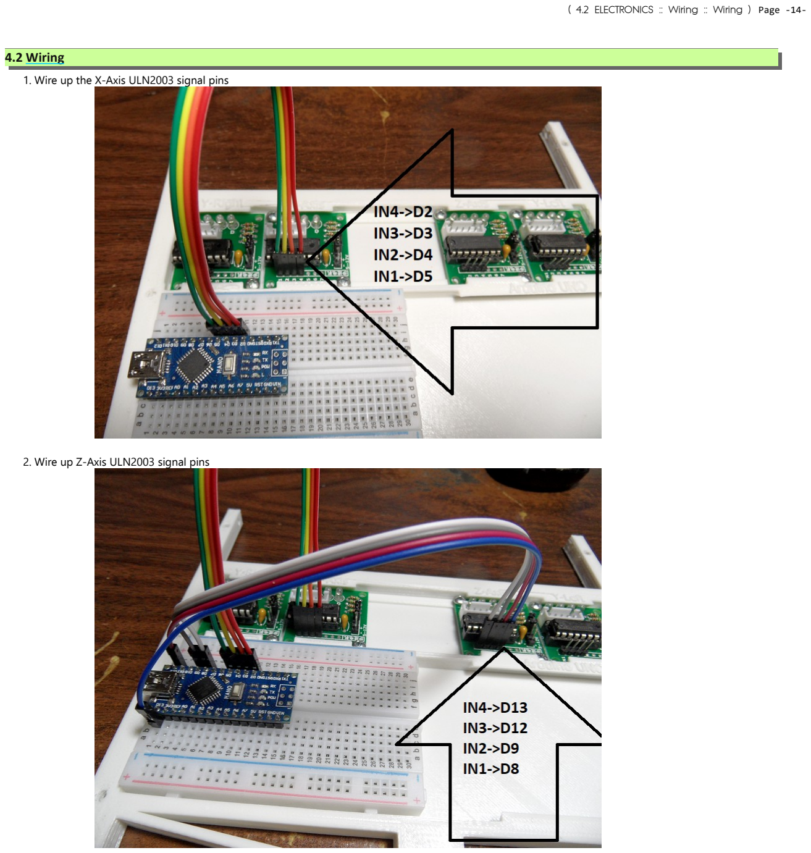
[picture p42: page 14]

( 4.2 ELECTRONICS :: Wiring :: Wiring ) Page -14-

### 4.2 Wiring

1. Wire up the X-Axis ULN2003 signal pins
2. Wire up Z-Axis ULN2003 signal pins

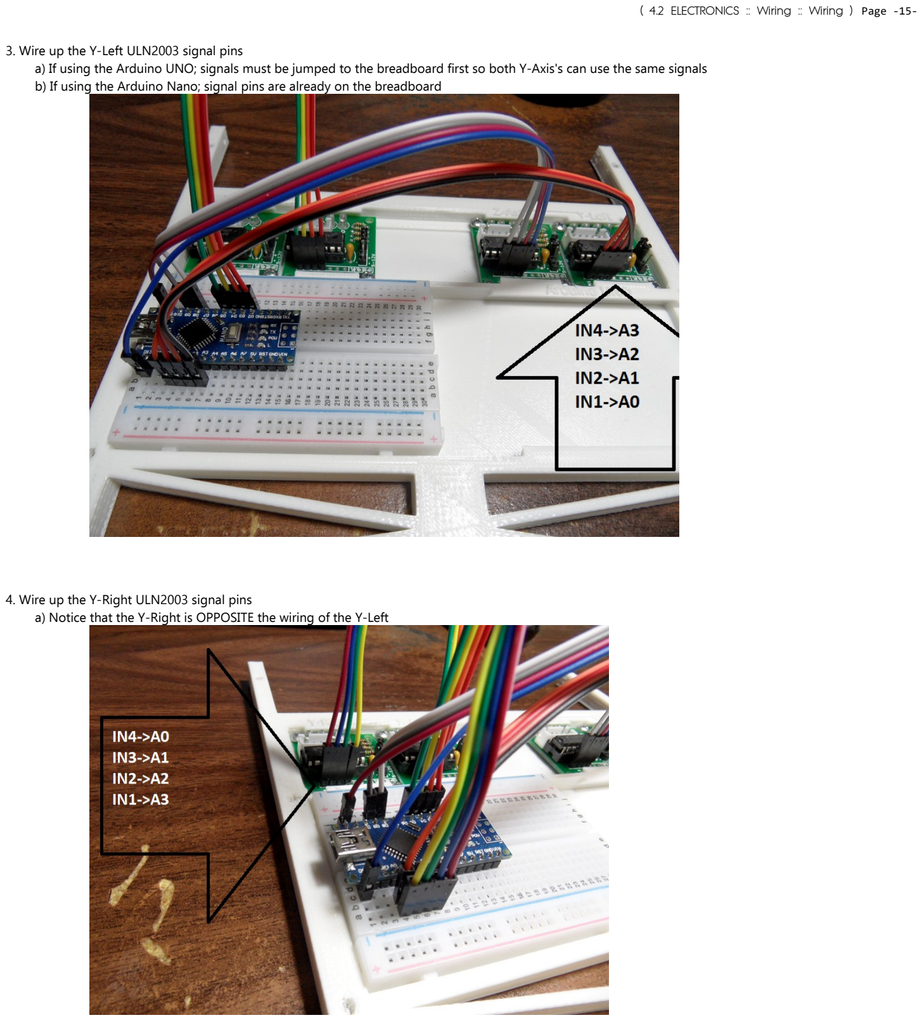
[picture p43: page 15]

( 4.2 ELECTRONICS :: Wiring :: Wiring ) Page -15-

3. Wire up the Y-Left ULN2003 signal pins
a) If using the Arduino UNO; signals must be jumped to the breadboard first so both Y-Axis's can use the same signals
b) If using the Arduino Nano; signal pins are already on the breadboard
4. Wire up the Y-Right ULN2003 signal pins
a) Notice that the Y-Right is OPPOSITE the wiring of the Y-Left

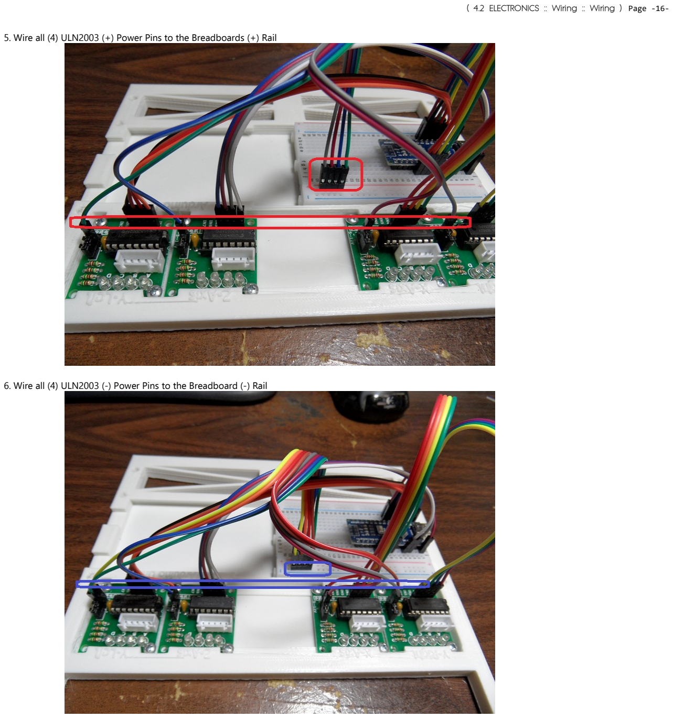
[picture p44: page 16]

( 4.2 ELECTRONICS :: Wiring :: Wiring ) Page -16-

5. Wire all (4) ULN2003 (+) Power Pins to the Breadboards (+) Rail
6. Wire all (4) ULN2003 (-) Power Pins to the Breadboard (-) Rail

( 4.2 ELECTRONICS :: Wiring :: Wiring ) Page -17-

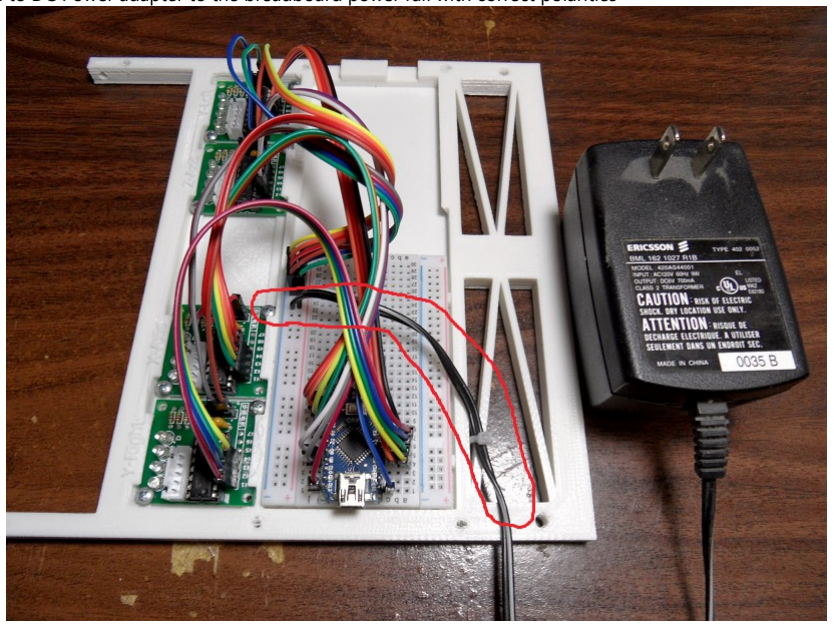
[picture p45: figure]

7. Wire the AC to DC Power adapter to the breadboard power rail with correct polarities

( 4.2 ELECTRONICS :: Wiring :: Wiring ) Page -18-

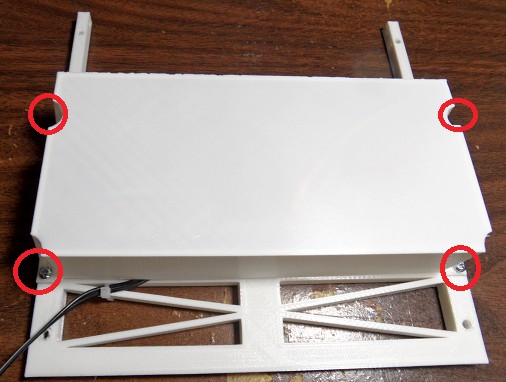
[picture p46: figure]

8. Using #6 x 3/8” Sheet Metal Screws; Attach the Backcover.stl

( 4.3 ELECTRONICS :: Wiring Diagram :: Wiring Diagram ) Page -19-

### 4.3 Wiring Diagram

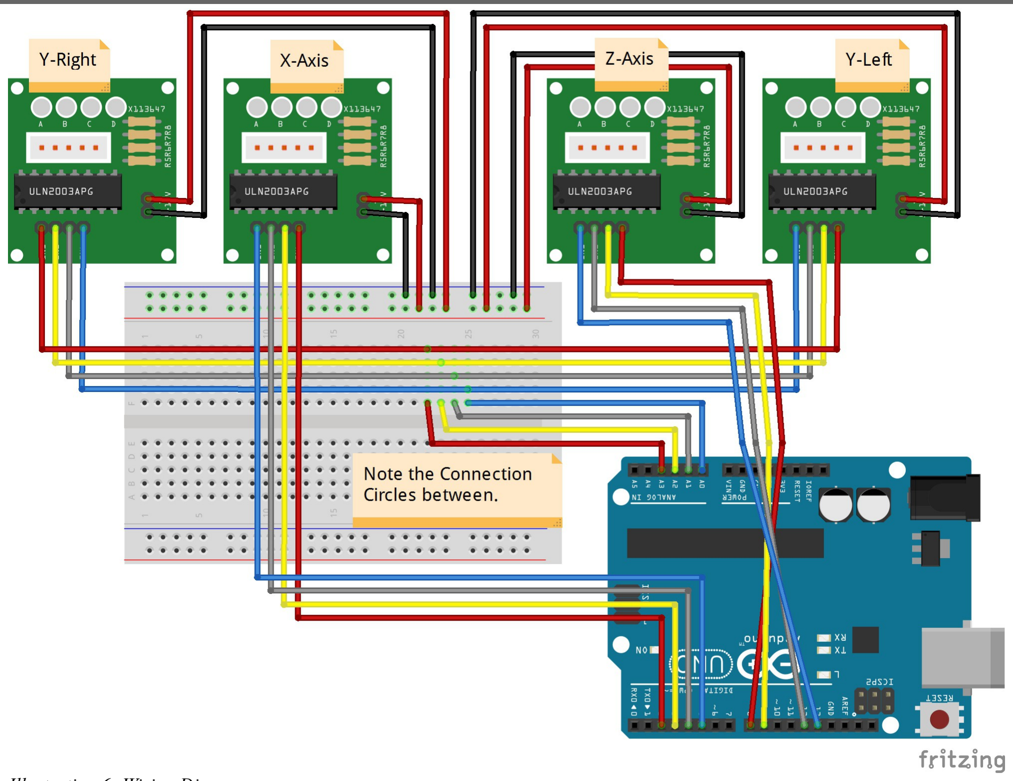
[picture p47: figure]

Illustration 6: Wiring Diagram

( 5. SOFTWARE / FIRMWARE :: SOFTWARE / FIRMWARE :: SOFTWARE / FIRMWARE ) Page -20-

### 5. SOFTWARE / FIRMWARE

### 5.1 Firmware Upload

1. Install Arduino Sketch IDE | https://www.arduino.cc/en/Main/Software
2. Install the modified GRB-28BYJ-48 Firmware
a) In a web-browser; go to https://github.com/tgit23/GRBL-28byj-48
b) Click on the file GRBL.ZIP
c) Click on the DOWNLOAD button on the lower-right next to “History” and Save to a place you'll remember – like Documents or Desktop
d) Run the Arduino Sketch IDE
e) Choose Menu Item SKETCH → INCLUDE LIBRARY → ADD .ZIP LIBRARY
f) Select the GRBL.ZIP Library file saved in step 'c' above
3. Upload the Firmware
a) Inside any running Arduino Sketch IDE
b) Choose FILE → EXAMPLES → GRBL → GRBLUPLOAD
c) Select the Port the Arduino UNO is connected to; in Sketch menu TOOLS → PORT
d) Select the Board; Sketch menu TOOLS → BOARD → ARDUINO/GENUINO UNO
e) Press the Up-Arrow in the Top-Left Corner to upload the firmware onto the Arduino UNO board
4. Now the unit is ready for operation.

✔ More Information
◌ GRBL Wiki @ https://github.com/gnea/grbl/wiki ◌

( 5.2 SOFTWARE / FIRMWARE :: Controller Install / Initial Settings :: Controller Install / Initial Settings ) Page -21-

### 5.2 Controller Install / Initial Settings

1. Download and install GRBL CONTROLLER located @ http://zapmaker.org/projects/grbl-controller-3-0/
2. Run GRBL CONTROLLER

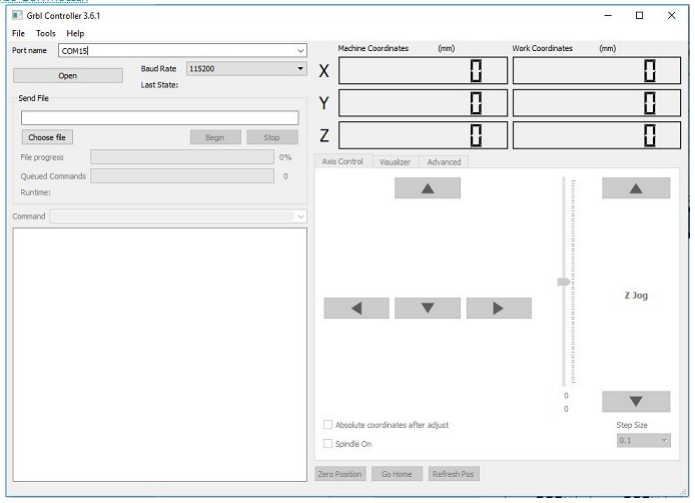
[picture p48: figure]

3. Pick the Port on which the Arduino UNO is connected and click 'Open'
4. Enter GRBL Settings for the Machine ( First Time Only )
a) $0=3 | ; Step pulse, microseconds
b) $1=1 | ; Step idle delay, microseconds ( shuts off motors )
c) $100=100 | ; X steps/mm
d) $101=100 | ; Y steps/mm
e) $102=100 | ; Z steps/mm
f) $110=550 | ; Max rate X, mm/min
g) $111=550 | ; Max rate Y, mm/min
h) $112=550 | ; Max rate Z, mm/min
i) $120=100 | ; X Acceleration, mm/sec^2
j) $121=100 | ; Y Acceleration, mm/sec^2
k) $122=100 | ; Z Acceleration, mm/sec^2

GRBL will store these values in the Arduino UNO EEPROM thus retain them during during power off and uploads.

✔ In 3d printer terms the GUI Controller example would be 'pronterface'.

### 5.3 Running a design file

1. Run GRBL CONTROLLER
2. Pick the Port on which the Arduino UNO ( Machine ) is connected and click 'Open'
3. On Tab 'Axis Control' select 'Step Size' 10 and then click the up-arrow on Z-Jog.
4. Using the 'Axis Control' to operate the machine motion; position the 'head' at a point that will be represented as coordinate 0,0
5. Click 'Zero Position'
6. Under 'Send File' click 'Choose File' and select the design file (.nc) to run

( 5.3 SOFTWARE / FIRMWARE :: Running a design file :: Running a design file ) Page -22-

a) Example files can be gotten @ https://github.com/tgit23/RPieces-TableTopXYZ/tree/master/nc-examples
7. Click 'Begin' to start executing.

### 5.4 Design Software

Design Software for GRBL often includes the G-Code generator ( In 3d printer terms – slic3r ).

✔ Common free GRBL design software ( the signifying difference being CAM or CAD ) ◌ FreeMill w/ VisualCAM (also free)
◌ SketchUCam plug-in for Google Sketchup
◌ pyCam

✔ Milling or drilling PCB
◌ KiCad
◌ FlatCAM

### 6. TOOL-HEADS

### 6.1 Pilot-Razor-Point-Pen

Illustration 7: ToolHead-PilotRazorPointPen.STL

✔ Example of the Pen @ http://www.staples.com/Pilot-Razor-Point-Pens/product_SS110064

✔ Mounting Hardware Required
◌ (1) #6-32 x 1/2” Machine Screw & Nut

### 6.2 Mini-Drill

** Not yet ready for Version 2.0 – Updates will come soon **

Illustration 8: ToolHead-PilotRazorPointPen.STL

✔ Example of Mini-Drill @ https://www.amazon.com/Lemonbest-Micro-Electric-Drill-1-5mm/dp/B01301L2L6/ref=pd_sim_60_3
◌ Full Description Line | Mini DIY Micro Electric Hand Drill for PCB 0.7 to 1.5mm Craft Drill Chuck Tools with US Plug
◌ Item Weight | 2.7 ounces
◌ Product Dimensions | 5.1 x 1 x 1 inches
◌ Wattage | 18 watts

✔ Mounting Hardware Required
◌ (3) #6-32 x 1-1/2” ( or Longer ) Machine Screws

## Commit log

2017-02-20 Added 3d printed pieces
    [BackSide.skp, Leg.skp, MotorGear.skp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]
2017-02-20 Added STL and Sketchup Model Files
    [BackSide.skp, BackSide.stl, Leg.skp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]
2017-02-26 Added new pieces and made changes to existing
    [BackSide.skp, BackSide.stl, Base-Front.skp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]
2017-02-27 Gear teeth adjustments
    [BackSide.stl, Base-Left.stl, Base-Right.stl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]
2017-02-28 Added a 2-member X-Guide
    [MotorGear.skp, X-LowerGuide.skp, X-LowerGuide.stl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]
2017-03-02 New gear design added
    [MotorGear.skp, MotorGear.stl, Wrench_for_No6.skp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]
2017-03-04 Z-Tool members & X-Guide added
    [ToolHead-PilotRazorPointPen.skp, ToolHead-PilotRazorPointPen.stl, ToolHead-Template.skp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]
2017-03-06 Update video, Fine tuning, docs
    [BackSide.skp, BackSide.stl, X-Guide.skp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]
2017-03-06 Added wiring diagram
    [WiringDiagram.fzz]
2017-03-07 User docs created
    [Base-Front.skp, Base-Left.skp, Base-Right.skp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]
2017-03-07 Updated docs made ToolHead folder.
    [ToolHead-PilotRazorPointPen.skp, ToolHead-PilotRazorPointPen.stl, ToolHead-Template.skp]
2017-03-09 Doc update & Mini Drill Tool-head
    [BackSide.skp, BackSide.stl, ToolHead-MiniDrill.skp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]
2017-03-11 Removed multiple Y-Racks updated docs
    [BackSide.skp, BackSide.stl, X-Rack-GuideMount.stl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]
2017-03-11 Fixed Y-MotorMount.stl
    [Leg.skp, Leg.stl, ToolHead-PilotRazorPointPen.stl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]
2018-03-04 New Models for Version 2.0
    [BackSide.skp, BackSide.stl, Base-Front.skp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]
2018-03-06 Initial working model
    [BackSide.skp, BackSide.stl, Full-Side.skp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]
2018-03-11 Version 2.0 Beta
    [Back.skp, Back.stl, BackCover.skp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]
